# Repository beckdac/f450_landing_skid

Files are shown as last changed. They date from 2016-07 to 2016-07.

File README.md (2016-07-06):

# f450_landing_skid
## Landing skid for F450 made from 3d printed parts and carbon fiber arrow shafts
---

Landing skid for F450 style quad.  Designed in OpenSCAD.  Latest version will always be on github: https://github.com/beckdac/f450_landing_skid
* Checkout https://github.com/chadkirby/BezierScad in this directory.  

I used carbon fiber arrow shafts for the cross bars after stripping the fletching, nock, and tips, e.g. https://www.amazon.com/gp/product/B00PDAOHPQ .  The padding is pipe insulation from the local hardware store wrapped with warning tape.

Printed with 20% infill in PLA.  The idea is that this should break first, absorbing the impact of a hard landing, and not your quad.  The whole rig with arrow shafts and 3d printed parts weighs 64g  (56 for the printed parts).  I broke a set of skids in a 40 foot fall but the quad was fine, otherwise.  Gives about 13.5cm vertical landing clearance with 16cm width between skids.

Images...
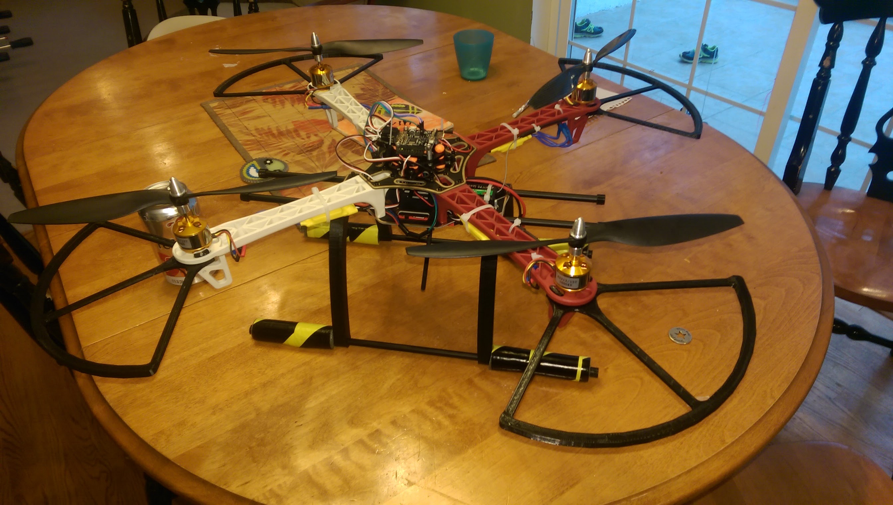
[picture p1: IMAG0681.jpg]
overview

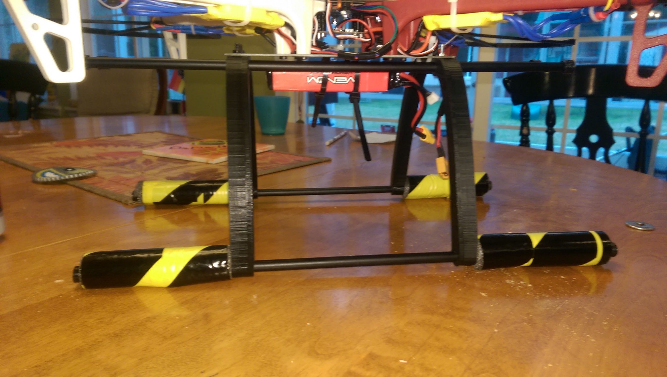
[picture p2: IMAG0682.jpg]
side

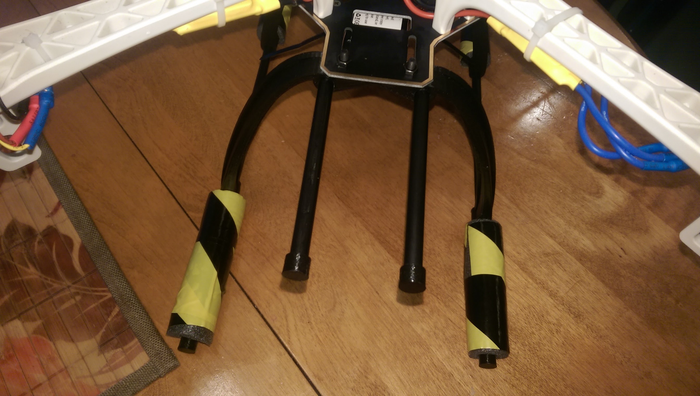
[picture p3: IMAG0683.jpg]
front


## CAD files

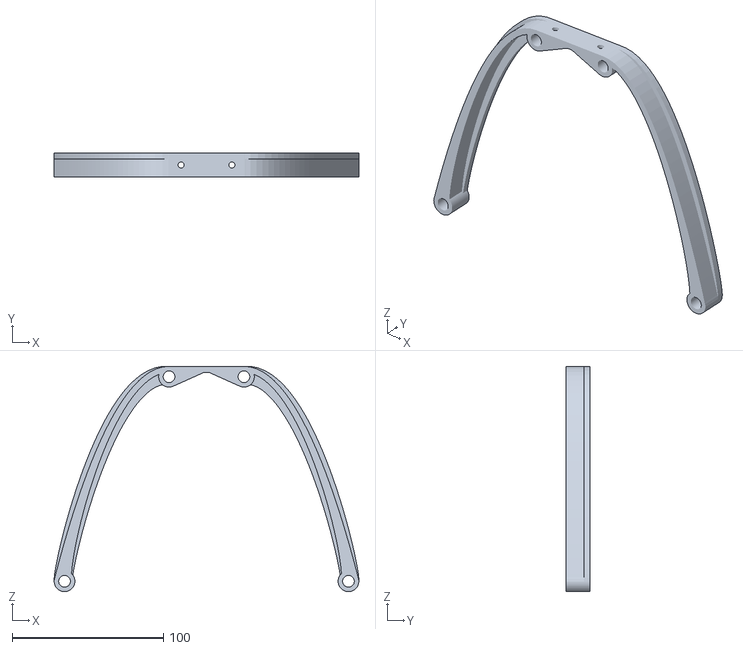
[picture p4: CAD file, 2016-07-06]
f450LandingSkid.stl
201.5 x 16.0 x 148.8

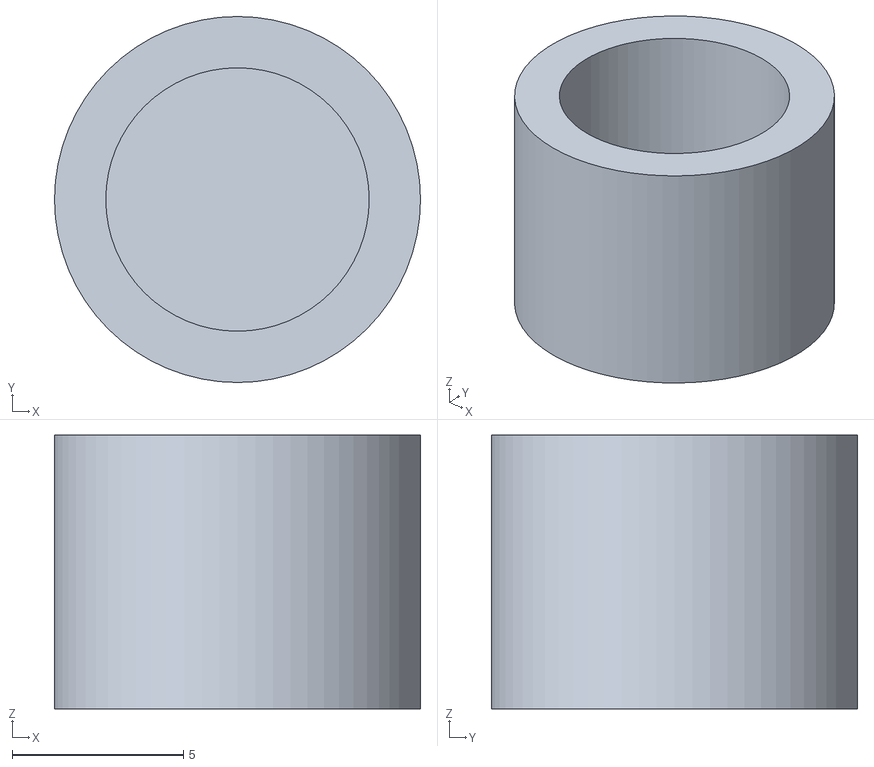
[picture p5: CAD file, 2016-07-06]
arrowCap.stl
10.7 x 10.7 x 8.00

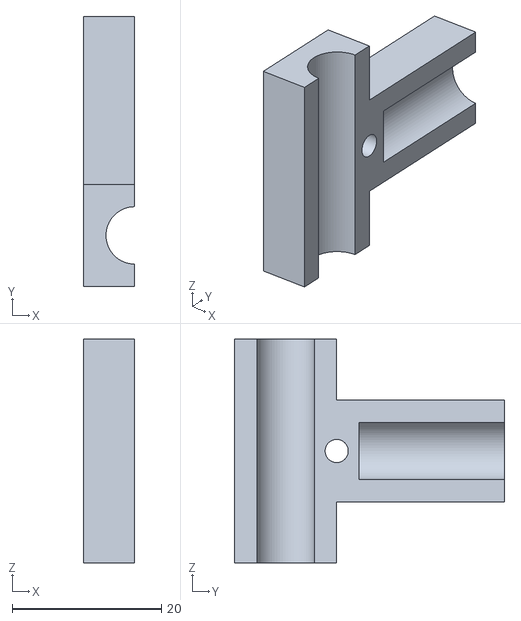
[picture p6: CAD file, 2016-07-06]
tFitting.stl
6.80 x 36.2 x 30.0

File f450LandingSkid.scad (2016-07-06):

// Requires OpenSCAD 2016.3+
use <BezierScad/BezierScad.scad>;

/* [Main] */

// select part
//part = "assembly";
//part = "tFitting";
//part = "arrowShaft";
part = "mountPlate";
//part = "shaftCap";

/* [Misc] */
plateThickness = 4;	// thickness of mount plate
partThickness = 3;	// thickness of walls (not mount plate) 
iFitAdjust = .4;	// interference fit adjustment for 3D printer
cylHeightExt = .1;	// for overcutting on differences so they render correctly, nothing more, some small positive value
M3D = 3.1;			// M3 screw diameter
// render quality
$fn = 64; // [24:low quality, 48:development, 64:production]

/* [tFitting] */
tFittingCaptureLength = 30;

/* [arrowShaft] */
arrowShaftOD = 7.7;
arrowShaftThickness = 1;
arrowShaftID = arrowShaftOD - 2 * arrowShaftThickness;

/* [mountPlate] */
mountPlateScrewD = 4;
mountPlateScrewSep = 33.5; // tbm
skidHeight = 140;
arrowShaftCurveTrans = .17;
// below taken from https://www.metricmcc.com/catalog/Ch1/1-32.pdf
mountPlateScrewCapD = 7 + iFitAdjust;
mountPlateScrewCapHeight = 4;


/* [shaftCap] */
shaftCapLength = 8;


render_part();

module render_part() {
	if (part == "assembly") {
		assembly();
	} else if (part == "tFitting") {
		tFitting();
	} else if (part == "arrowShaft") {
		arrowShaft();
	} else if (part == "mountPlate") {
		mountPlate();
	} else if (part == "shaftCap") {
		shaftCap();
	} else {
		// invalid value
	}
}

module assembly() {
	//arrowShaft(100);
	//tFitting();
	mountPlate();
}


module shaftCap() {
		difference() {
			cylinder(d=arrowShaftOD + partThickness,
				h=shaftCapLength, center=true);
			translate([0, 0, partThickness / 2])
				cylinder(h=shaftCapLength + cylHeightExt,
					d=arrowShaftOD, center=true);
		}
}

module tFitting() {
  difference() {
	union() {
		/* horizontal of T */
		difference() {
			cube([arrowShaftOD + 2 * partThickness,
				arrowShaftOD + 2 * partThickness,
				tFittingCaptureLength], center=true);
			cylinder(h=tFittingCaptureLength + cylHeightExt,
				d=arrowShaftOD, center=true);
		}
		/* perpendicular */
		difference() {
		  translate([0,
				tFittingCaptureLength / 4 + ((arrowShaftOD + 2 * partThickness) / 2),
				0])
		   rotate([90, 0, 0])
			difference() {
				cube([arrowShaftOD + 2 * partThickness,
					arrowShaftOD + 2 * partThickness,
					tFittingCaptureLength], center=true);
				cylinder(h=tFittingCaptureLength + cylHeightExt,
					d=arrowShaftOD, center=true);
			}
		 // remove T
		 cylinder(h=tFittingCaptureLength + cylHeightExt,
				d=arrowShaftOD + 2 * partThickness, center=true);
		}
		translate([0, partThickness + arrowShaftOD / 2, 0])
		rotate([0, 90, 0]) {
			cube([arrowShaftOD + 2 * partThickness,
				2 * partThickness,
				arrowShaftOD + 2 * partThickness], center=true);
		}
	}
			translate([(arrowShaftOD + 2 * partThickness) / 2
					- iFitAdjust / 2
					,
				arrowShaftOD + 2 * partThickness,
				0])
			cube([arrowShaftOD + 2 * partThickness + cylHeightExt,
				3.2 * (arrowShaftOD + 2 * partThickness),
				tFittingCaptureLength * 1.1], center=true);
		translate([0, partThickness + arrowShaftOD / 2, 0])
			rotate([0, 90, 0])
				cylinder(h=arrowShaftOD + 2 * partThickness + cylHeightExt,
					d=M3D, center=true);
  }
}

module arrowShaft(arrowShaftLength) {
	difference() {
		cylinder(h=arrowShaftLength, d=arrowShaftOD, center=true);
		cylinder(h=arrowShaftLength + cylHeightExt, d=arrowShaftID, center=true);
	}
}

module mountPlate() {
	difference() {
		union() {
			cube([mountPlateScrewSep + 4 * mountPlateScrewD,
				4 * mountPlateScrewD,
				plateThickness], center=true);
			for (i = [-1,1]) {
			 difference() {
			  union() {
				translate([i * (mountPlateScrewSep + 4 * mountPlateScrewD) /2, 
						mountPlateScrewD * 2, 0])
					rotate([90, 0, 0]) {
						BezWall([
								[0, 0],
								[i * skidHeight / 3.5, 0],
								[i * skidHeight / 2, -skidHeight * .9],
								[i * skidHeight / 2, -skidHeight]
							], widthCtls = [plateThickness, plateThickness, plateThickness, 3 * plateThickness ],
							height = 4 * mountPlateScrewD, steps = 32, centered=true);
					}
				// bracing arm
				translate([i * (mountPlateScrewSep + 4 * mountPlateScrewD) /2, 
						mountPlateScrewD * 2, 0])
					rotate([90, 0, 0]) {
						BezWall([
								[0, - plateThickness],
								[i * skidHeight / 3.5, 0],
								[i * skidHeight / 2, -skidHeight * .9],
								[i * skidHeight / 2, -skidHeight]
							], widthCtls = [3 * plateThickness, 3 * plateThickness, 3 * plateThickness, 3 * plateThickness ],
							height =  plateThickness, steps = 32, centered=true);
					}
				translate([i * skidHeight / 2 + i * skidHeight * (arrowShaftCurveTrans), 
						0, -skidHeight])
					rotate([90, 0, 0]) {
						difference() {
							cylinder(h=4 * mountPlateScrewD,
								d=arrowShaftOD + 2 * partThickness, center=true);
							cylinder(h=4 * mountPlateScrewD + cylHeightExt,
							d=arrowShaftOD, center=true);
						}
					}
			  }
				translate([i * skidHeight / 2 + i * skidHeight * (arrowShaftCurveTrans), 
						0, -skidHeight])
					rotate([90, 0, 0]) {
							cylinder(h=4 * mountPlateScrewD + cylHeightExt,
							d=arrowShaftOD, center=true);
					}
			 }
			}
			/* horizontal of T */
			for (i = [-1, 1])
				translate([i * (mountPlateScrewSep + 4 * mountPlateScrewD) / 2,
					0, plateThickness / 2  -(arrowShaftOD + 2 * partThickness) / 2])
				rotate([90, 0, 0])
				difference() {
					hull() {
						cylinder(h=4 * mountPlateScrewD,
							d=arrowShaftOD + 2 * partThickness, center=true);
						translate([-i * (8 * mountPlateScrewD),
								(arrowShaftOD + 2 * partThickness) / 2,
								0])
							#cylinder(h=4 * mountPlateScrewD,
								d=.00001, center=true);
					}
					cylinder(h=4 * mountPlateScrewD + cylHeightExt,
						d=arrowShaftOD, center=true);
			}
		}
		for (i=[-1, 1]) {
			translate([i * mountPlateScrewSep / 2, 0, 0])
				cylinder(h=plateThickness * 10 + cylHeightExt, d=mountPlateScrewD, center=true);
			translate([i * mountPlateScrewSep / 2, 0, - 2.5 * plateThickness])
				cylinder(h=mountPlateScrewCapHeight * 2, d=mountPlateScrewCapD, center=true);
		}
		for (i = [-1, 1])
			translate([i * (mountPlateScrewSep + 4 * mountPlateScrewD) / 2,
				0, plateThickness / 2  -(arrowShaftOD + 2 * partThickness) / 2])
			rotate([90, 0, 0])
					cylinder(h=4 * mountPlateScrewD + cylHeightExt,
						d=arrowShaftOD, center=true);
	}
}

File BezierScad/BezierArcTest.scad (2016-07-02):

use <BezierScad.scad>;

BezArc([
  [-10,-1],
  [-10, -6],
  [-1, -1],
  [-5, -10],
  [-1,-10]
  ], [-1,-1], steps = 32, heightCtls = [1,2,10,2,1]);

difference() {
translate([25,0,0]) 
    BezArc([
      [-10, 0],
      [-10, -6],
      [-1, -1],
      [-5, -10],
      [0,-10]
      ], focalPoint = [0,0], steps = 30, heightCtls = [5,7,8,7,5]);
 translate([28,0,0]) 
    BezArc([
      [-10, 0],
      [-10, -6],
      [-1, -1],
      [-5, -10],
      [0,-10]
      ], focalPoint = [0,0], steps = 30, heightCtls = [6,8,9,8,6]);
}

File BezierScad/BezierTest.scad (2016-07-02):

use <BezierScad.scad>;
x = 25;

translate([7.5,0,0]) 
BezWall( [
  [0,0],
  [x/2, x],
  [x,0],
] , width = 1.5, height = 10, steps = 4, centered = true );

translate([37.5,0,0]) 
BezWall( [
  [0,0],
  [0, x], [x, x],
  [x,0],
] , width = 1.5, height = 10, steps = 6, centered = true );

translate([67.5,0,0]) 
BezWall( [
  [0,0],
  [0, x], [x/2, x], [x, x],
  [x,0],
] , width = 1.5, height = 10, steps = 8, centered = true );

translate([97.5,0,0]) 
BezWall( [
  [0,0],
  [0, x], [0, x], [x, x], [x, x],
  [x,0],
] , width = 1.5, height = 10, steps = 10, centered = true );

translate([127.5,0,0]) 
BezWall( [
  [0,0],
  [0, x], [0, x], [x/2, x], [x, x], [x, x],
  [x,0],
] , width = 1.5, height = 10, steps = 12, centered = true );

translate([157.5,0,0]) 
#BezWall( [
  [0,0],
  [0, x], [0, x], [0, x], [x, x], [x, x], [x, x],
  [x,x/2],
] , width = 2.5, height = 4, steps = 32, centered = true );

BezWall([
  [-0.1,0],
  [-20, 0],
  [-25,25]
  ],  widthCtls = [10, 1], 
      heightCtls = [1, 5, 6, 35], 
      steps = 32,
      centered = true
);
translate([0,30,0])
BezWall([
  [-0.1,0],
  [-15, 0],
  [-15, 25],
  [-25,25]
  ],  
    width = 2, 
    heightCtls = [1, 35, 1], 
    steps = 16,
    centered = false
);

translate([-30,30,0])
BezWall([
  [-0.1,0],
  [-15, 0],
  [-15, 25],
  [-25,25]
  ],  
    widthCtls = [2, 10], 
    height = 5, 
    steps = 16,
    centered = true
);

linear_extrude(height = 5) 
BezLine([
  [0,-10], [5, -20], [0,-30]
  ], width = [5, 10], resolution = 2, centered = true);

linear_extrude(height = 5) 
BezLine([
  [0,10], [5, 20], [0,30]
  ], width = [5, 10], resolution = 3, centered = false);

translate([-10, -10,0])
BezArc([
  [-10,-1],
  [-10, -10],
  [-1,-10]
  ], [-1,-1], steps = 16, heightCtls = [1,10]);

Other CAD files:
BezierScad/BezierScad.scad

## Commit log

2016-07-01 prototype tFitting
    [f450LandingSkid.scad]
2016-07-01 beta mount
    [f450LandingSkid.scad]
2016-07-02 added BezierScad library to make BezierWalls
    [BezierArcTest.scad, BezierScad.scad, BezierTest.scad]
2016-07-02 prototype complete
    [f450LandingSkid.scad]
2016-07-02 printable prototype ready
    [f450LandingSkid.scad]
2016-07-02 strengthened prototype
    [f450LandingSkid.scad]
2016-07-06 added in STLs
    [arrowCap.stl, f450LandingSkid.stl, tFitting.stl]
2016-07-06 added default render to be the arms (called mount plate)
    [f450LandingSkid.scad]
